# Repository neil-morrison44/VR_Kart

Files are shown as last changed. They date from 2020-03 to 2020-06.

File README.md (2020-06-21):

# VR_Kart

A 3D Printed Raspberry PI powered car with an a-frame VR interface

| | | |
| --- | --- | --- |
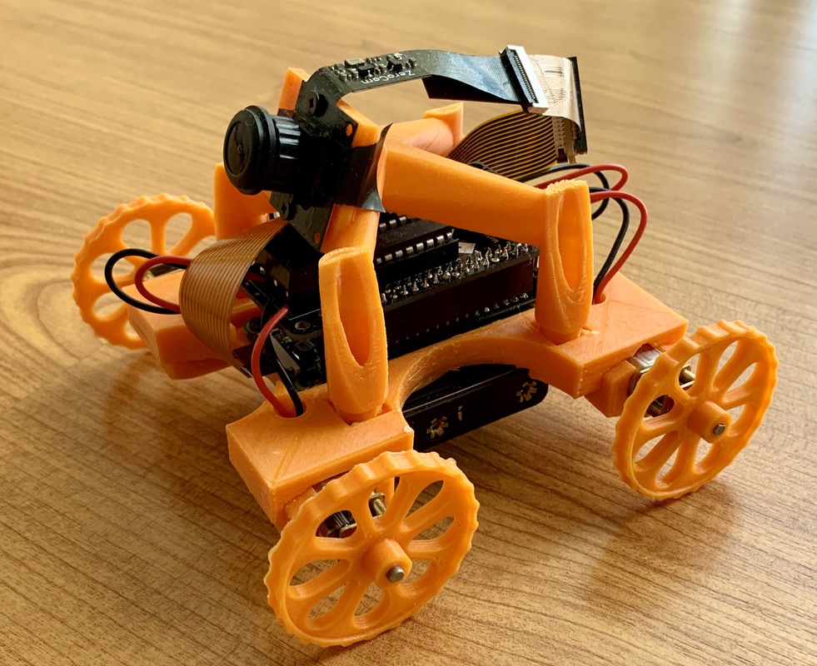
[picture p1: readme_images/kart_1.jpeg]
Kart Image 1
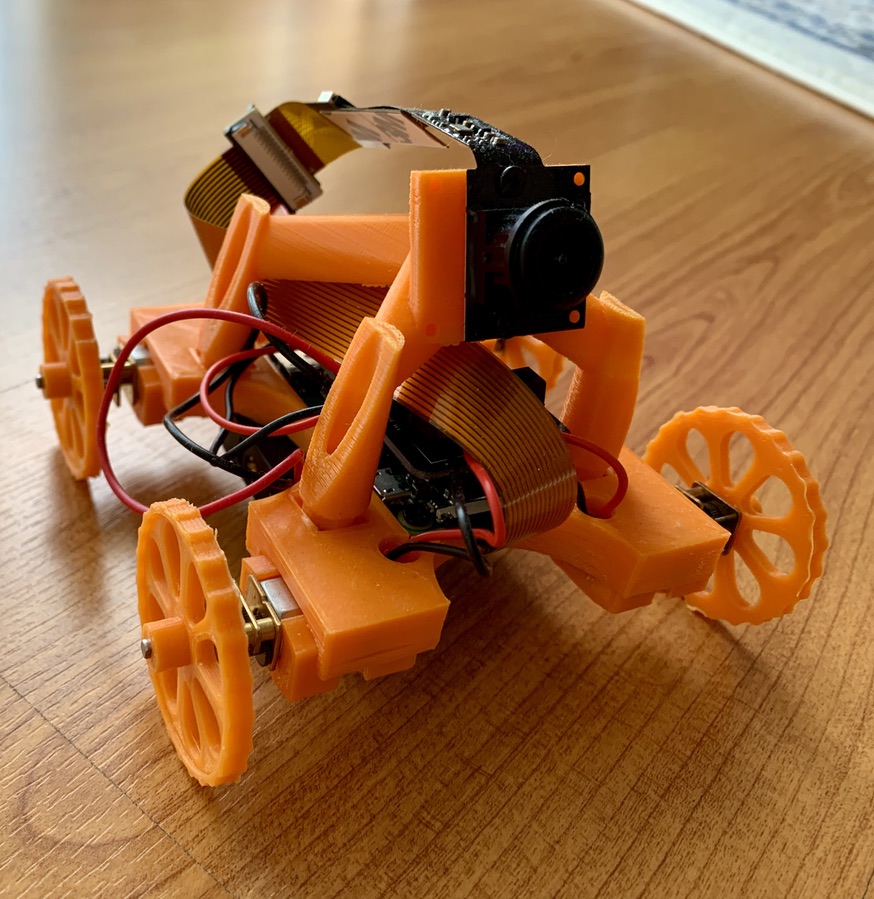
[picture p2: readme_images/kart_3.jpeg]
Kart Image 3
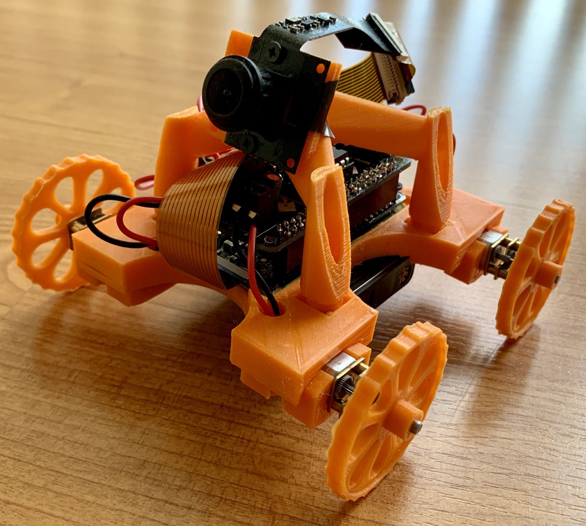
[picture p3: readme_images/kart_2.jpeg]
Kart Image 2
|  |  |  |

## Part List

| part | notes | link |
| --- | --- | --- |
| Pi Zero W | A bit underpowered for this | https://thepihut.com/products/raspberry-pi-zero-w |
| MotoZero | | https://thepihut.com/products/motozero |
| ZeroCam FishEye | | https://thepihut.com/products/zerocam-fisheye-camera-for-raspberry-pi-zero  |
| N20 DC 6V 150RPM | | https://www.amazon.co.uk/gp/product/B07P55RLX5 |
| Pi Wide Input Shim | | https://thepihut.com/products/wide-input-shim |
| 4 AAA Battery Holder | Meant to buy a AA battery holder | https://www.amazon.co.uk/gp/product/B07KN2P7PD/ |
| Camera Cable Joiner | See notes | https://thepihut.com/products/camera-cable-joiner-extender-for-raspberry-pi |
| Camera Cable Adapter | See notes | https://shop.pimoroni.com/products/camera-cable-adapter |
| Camera Cable - Pi Zero edition | See Notes | https://shop.pimoroni.com/products/camera-cable-raspberry-pi-zero-edition |
| Misc 2.5mm / 3mm screws | | |

## Software Setup

- Install uv4l
- Install `rng-tools` otherwise node won't start until the stored entropy is large enough (which is slow when headless & USB device-less)

## Notes

### Camera extension cables

It turned out that the Zero camera's cable is the other way up than I thought - so I needed to loop around taking it up over the kart then down into the camera port. This means the camera mounting bit is missing screw holes on the side where the camera sits, hence the tape in the images.

### AA batteries

I ordered an AAA battery holder instead of an AA holder accidentally, meaning the mAh are capped around 800 rather than the ~2000 mAh you could get from an AA battery. The design would need to be larger to allow for an AA holder.

### Cable connections

Cables from the batteries go into the MotoZero board, with other cables running from the same input screw terminals to the Pi Wide Input shim. Should mean the Pi powers up when the batteries are put in.

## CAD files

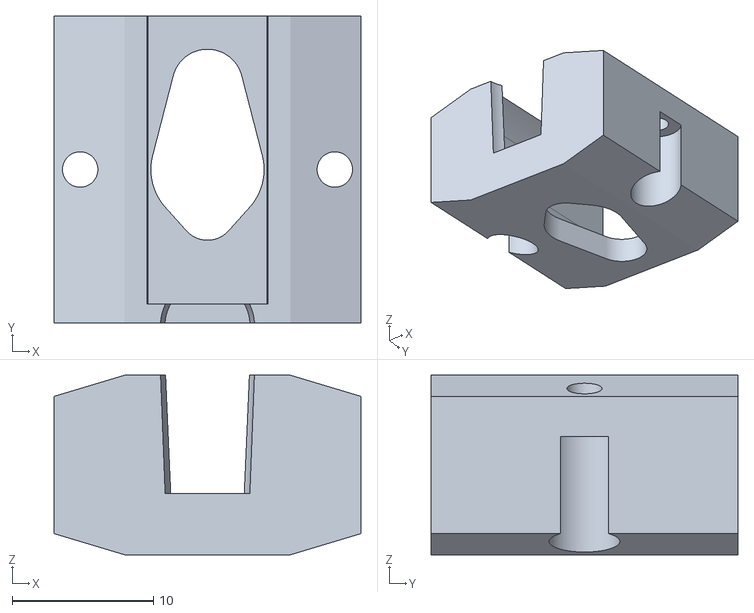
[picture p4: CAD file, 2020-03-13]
3D_models/motor_holder.stl
21.7 x 21.7 x 12.7

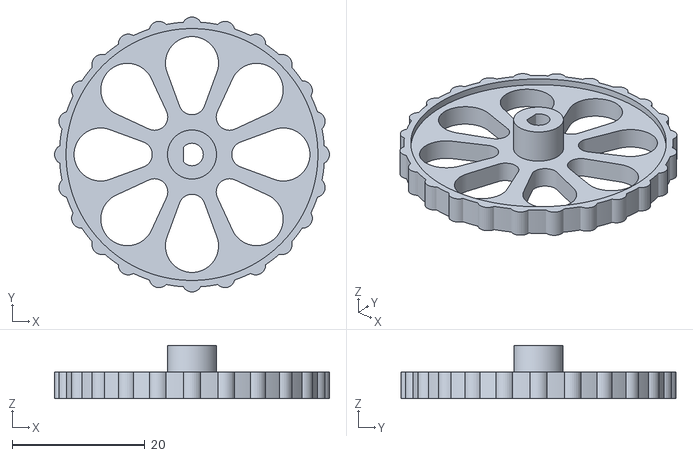
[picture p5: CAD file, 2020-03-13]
3D_models/wheel.stl
41.5 x 41.5 x 8.00

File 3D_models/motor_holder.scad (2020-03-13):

$screwHole = 1.25;
$fa = 1;
$fs = 0.1;

$motorLength = 21.5;
$motorPadding = 0.25;
$bodyPadding = -0.3;

module motorAttachCutout(){

  hull(){
    cube([22 + $bodyPadding, 22 + $bodyPadding, 10 + $bodyPadding], true);
    cube([12 + $bodyPadding, 22 + $bodyPadding, 13 + $bodyPadding], true);
  }
}

module motorWirepath(){
  translate([0, -11, -2])
    cylinder(13,3,3.5);
}

module screwHoles(){
  translate([9, 0, -2])
    cylinder(10, $screwHole, $screwHole);
  translate([-9, 0, -2])
    cylinder(10, $screwHole, $screwHole);
}

module screwPaths(){
  translate([9, 0, -8])
    cylinder(10, $screwHole * 2, $screwHole * 2);
  translate([-9, 0, -8])
    cylinder(10, $screwHole * 2, $screwHole * 2);
}

module motorCutout(){
  rotate([90,0,0]){
  intersection(){
    cylinder($motorLength, 6.5 + ($motorPadding / 2), 6.5 + ($motorPadding / 2));
    translate([0,0, $motorLength / 2])
      cube([12.1 + $motorPadding, 10 + $motorPadding, $motorLength], true);
  }
  }
}

module airHoles(){
  hull(){
  translate([0,0,-10]){
    cylinder(20, 4, 4);
    translate([0, 6, 0])
      cylinder(20, 2.5, 2.5);
    translate([0, -3, 0])
      cylinder(20, 2, 2);
  }
}
}

difference(){
  motorAttachCutout();
  screwHoles();
  screwPaths();
  motorWirepath();
  translate([0, 12, 1.3])
    motorCutout();
  airHoles();
}

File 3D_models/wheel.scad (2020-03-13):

$fa = 0.5;
$fs = 0.1;
$radius = 20;
$shaftRadius = 1.7;
$thickness = 2;
$gripCount = 24;
$rimHeight = 1;
$wheelHeight = 3;
$screwHole = 1.25;
$shaftHeight = 120;
$hubHeight = 5;
$gripThickness = 1.5;

module wheelBase(){
  cylinder($wheelHeight,$radius,$radius);
  cylinder($wheelHeight + $hubHeight,$shaftRadius + $thickness,$shaftRadius + $thickness);
}

module wheelGrips(){
  $fa = 12;
  for (i=[1:$gripCount]){
    rotate([0, 0, (360 / $gripCount) * i ]){
      translate([$radius - ($gripThickness / 2), 0, 0]){
        cylinder($wheelHeight + $rimHeight,$gripThickness,$gripThickness);
      }
    }
  }
}

module wheelRim(){
  difference(){
    union(){
      wheelGrips();
      cylinder($rimHeight + $wheelHeight,$radius,$radius);
    }
    cylinder(20,$radius - 1,$radius - 1);
  }
}

module shaft(){
  translate([0, 0, -1])
    cylinder($wheelHeight + $hubHeight + 2, $shaftRadius, $shaftRadius);
}

module wheelHoles(){
  for (i=[1:8]){
    hull(){
    rotate([0, 0, (360 / 8) * i ]){
      translate([$radius / 1.45, 0, -1]){
        cylinder($wheelHeight * 2,$radius / 5, $radius / 5);
      }
    }
    rotate([0, 0, (360 / 8) * i ]){
      translate([$radius / 2.5, 0, -1]){
        cylinder($wheelHeight * 2,$radius / 10, $radius / 10);
      }
    }
  }
  }
}


module screwHole(){
  translate([0,0,$wheelHeight + ($hubHeight / 2)]){
    rotate([0,90,0]){
      cylinder(10, $screwHole, $screwHole);
    }
  }
}

module block(){
  translate([-2.3,0,($hubHeight + $wheelHeight) / 2]){
    cube([2, 2.2, ($hubHeight  + $wheelHeight)], true);
  }
}


difference(){
  union(){
    wheelBase();
    wheelRim();
    
  }
  shaft();
  wheelHoles();
}

block();

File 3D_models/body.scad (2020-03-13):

$fs = 0.01;
$fa = 1;

$wheelDepth = 5.5;
$bodyLength = 100;
$bodyWidth = 75;
$bodyDepth = 10;
$screwHole = 1.25;

module mainBody(){
  cube([$bodyLength,$bodyWidth,$bodyDepth], true);
}

module batteryCutout(){
  translate([0,0,-5])
    cube([50,52,5], true);
  translate([15,-30,-5])
    cube([10, 20, 5], true);
  translate([18, 0, -10])
    cylinder(10,$screwHole,$screwHole);
  translate([-18, 0, -10])
    cylinder(10,$screwHole,$screwHole);
}



module motorAttachCutout(){
  translate([9, 0, -2])
    cylinder(10,$screwHole,$screwHole);
  translate([-9, 0, -2])
    cylinder(10,$screwHole,$screwHole);
  hull(){
    cube([22, 22, 10], true);
    cube([12, 22, 13], true);
  }
  translate([0, -11, -2])
    cylinder(13,3,3.5);
}

module motorOne(){
  translate([37, 30, -$wheelDepth])
    motorAttachCutout();
}

module motorTwo(){
  translate([37, -30, -$wheelDepth])
    rotate([0,0,-180])
      motorAttachCutout();
}

module motorThree(){
  translate([-38, 30, -$wheelDepth])
    motorAttachCutout();
}

module motorFour(){
  translate([-38, -30, -$wheelDepth])
    rotate([0,0,-180])
      motorAttachCutout();
}

module piCutout(){
  translate([0,0,5])
    cube([70, 32, 8], true);
  translate([0,12,5])
    cube([55, 8, 12], true);
  //improve these
  translate([29, 11.5, -2])
    cylinder(10,$screwHole,$screwHole);
  translate([29, -11.5, -2])
    cylinder(10,$screwHole, $screwHole);
  translate([-29, 11.5, -2])
    cylinder(10,$screwHole, $screwHole);
  translate([-29, -11.5, -2])
    cylinder(10,$screwHole, $screwHole);
}

module cameraHolderCutout(){
  translate([0,0,5])
    cube([10, 10, 4], true);
    translate([0,0,0])
      cylinder(5,$screwHole,$screwHole);
}

module cameraHolderCutouts(){
  translate([-25,-25,0])
    cameraHolderCutout();
  translate([25,-25,0])
    cameraHolderCutout();
  translate([-25,25,0])
    cameraHolderCutout();
  translate([25,25,0])
    cameraHolderCutout();

}

module wheelRodCutout(){
  translate([-38, 76 / 2, 0])
  rotate([90, 0, 0]){
    cylinder($bodyWidth + 1,3,3);
  }
}

module circleCutouts(){
  translate([0,$bodyWidth / 2,-10])
    cylinder(50,20,20);
   translate([0,-$bodyWidth / 2,-10])
    cylinder(50,20,20);
  translate([$bodyLength / 2,0,-10])
    cylinder(50,18,18);
  translate([-$bodyLength / 2,0,-10])
    cylinder(50,14,14);
}

module speedHoles(){
  hull(){
  translate([0,0,-5]){
    cylinder(10,4,8);
    translate([10,0,0])
      cylinder(10,4,8);
    translate([-10,0,0])
      cylinder(10,4,8);
  }}
}

difference(){
  mainBody();
  batteryCutout();
  motorOne();
  motorTwo();
  motorThree();
  motorFour();
  piCutout();
  cameraHolderCutouts();
  wheelRodCutout();
  circleCutouts();
  speedHoles();
}

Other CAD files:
3D_models/camera_holder.scad

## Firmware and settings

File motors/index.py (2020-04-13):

import socket
import time
import os
import json
from gpiozero import Motor, OutputDevice

socket_path = '/tmp/uv4l.socket'

try:
    os.unlink(socket_path)
except OSError:
    if os.path.exists(socket_path):
        raise

s = socket.socket(socket.AF_UNIX, socket.SOCK_SEQPACKET)

print('socket_path: ', socket_path)
s.bind(socket_path)
s.listen(1)


def setupMotors():
    motor1 = Motor(24, 27)
    motor1_enable = OutputDevice(5, initial_value=1)
    motor2 = Motor(6, 22)
    motor2_enable = OutputDevice(17, initial_value=1)
    motor3 = Motor(23, 16)
    motor3_enable = OutputDevice(12, initial_value=1)
    motor4 = Motor(13, 18)
    motor4_enable = OutputDevice(25, initial_value=1)
    return [motor1, motor2, motor3, motor4]


motors = setupMotors()


def cleanup():
    print("cleanup")
    for motor in motors:
        motor.stop()


while True:
    print('awaiting connection...')
    connection, client_address = s.accept()
    print('client_address:', client_address)
    try:
        print('established connection with', client_address)
        while True:
            data = connection.recv(128)
            print('received message: ', data)

            time.sleep(0.01)
            print(str(data)[2:-1])
            try:
                values = json.loads(str(data)[2:-1])

                for i in range(len(values)):
                    motors[i].value = values[i]
            except json.decoder.JSONDecodeError:
                print("JSON Error")

            if data:
                print('echo data to client')
                connection.sendall(data)
            else:
                print('no more data from', client_address)
                break

    finally:
        # Clean up the connection
        cleanup()
        connection.close()

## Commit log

2020-03-13 Add 3D Models
    [body.scad, camera_holder.scad, motor_holder.scad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]
2020-04-11 increase thread count
2020-04-12 start motors controller
2020-04-13 try python since node doesn't support seqpacket
    [index.py]
2020-04-13 add motor control
2020-04-13 better trap and handle errors
    [index.py]
2020-05-08 add wheel, grabs just now & it's on the controller rather than the wheel...
2020-05-09 make the wheel itself the collider so we can init a plane
2020-05-09 rotatable wheel
2020-05-11 Add throttle, having some hit clear issues
2020-05-17 Fix throttle sticking, calculate motor values
